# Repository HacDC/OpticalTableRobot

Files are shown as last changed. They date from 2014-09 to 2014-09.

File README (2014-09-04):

Copyright (C) 2013 mirage335
See the end of the file for license conditions.
See license.txt for OpticalTableRobot license conditions.

mirage335-site.dyndns.org

Advanced multi-tool factory based on OpenRail.

Intended to simultaneously operate multiple milling, laser, extrusion (FDM 3D Printing), and inkjet (powder 3D printing, 2D coloring) tools.

See render.png for assembly overview, or download free eDrawings viewer for further investigation.

Comparable to FlexReplicator, but on a massive scale with enhanced precision, thanks to HacDC's 800lbs OpticalTable. This is the kind of machine one might use to 3D print large herringbone power transmissions for lost PLA casting, or carry out a VLSI production run.

Mechanical loads are expected to be far below the table's damage threshold, allowing it to remain aligned to optical tolerances.

__FutureWork__
Openbuilds has intriguing ACME high-pitch threaded rod actuators. Unfortunately, no allowance for anti-backlash is made, so these are unlikely to be used.

Standard timing belts may prove inadeuate for such a large ultra-precise machine. Vectran rope is a possibe substitute.

OpenBuilds has discontinued hardcoat aluminum rails in favor of polycarbonate wheels. While little if any performance degradation is expected, these substitutions need to be reflected in CAD model materials and BOM data.

Supply chain issues are common to many parts in the BOM, secondary suppliers should be added.

__ReprapStatus__
Similarly to the FlexReplicator, a few 3D printed plastic brackets are used, and may be self-replicated. As rigidity was a primary concern, most components are metal, and not 3D printable.

However, unlike other RepRaps, this platform was explicitly designed for a variety of functionality, including CNC milling, PCB manufacture, and even semiconductor fabrication. Theoretically, one might manufacture intermediate equipment (eg. aluminum extruder, lathe).

__Copyright Extensions__
Files embedded into the design by mirage335 with a less restrictive license than GPLv3 place any derrived works under that license. This is definied to include any files pulled into the repository by mirage335 .

__Copyright__
This file is part of OpticalTableRobot.

OpticalTableRobot is free software: you can redistribute it and/or modify
it under the terms of the GNU General Public License as published by
the Free Software Foundation, either version 3 of the License, or
(at your option) any later version.

OpticalTableRobot is distributed in the hope that it will be useful,
but WITHOUT ANY WARRANTY; without even the implied warranty of
MERCHANTABILITY or FITNESS FOR A PARTICULAR PURPOSE.  See the
GNU General Public License for more details.

You should have received a copy of the GNU General Public License
along with OpticalTableRobot.  If not, see <http://www.gnu.org/licenses/>.

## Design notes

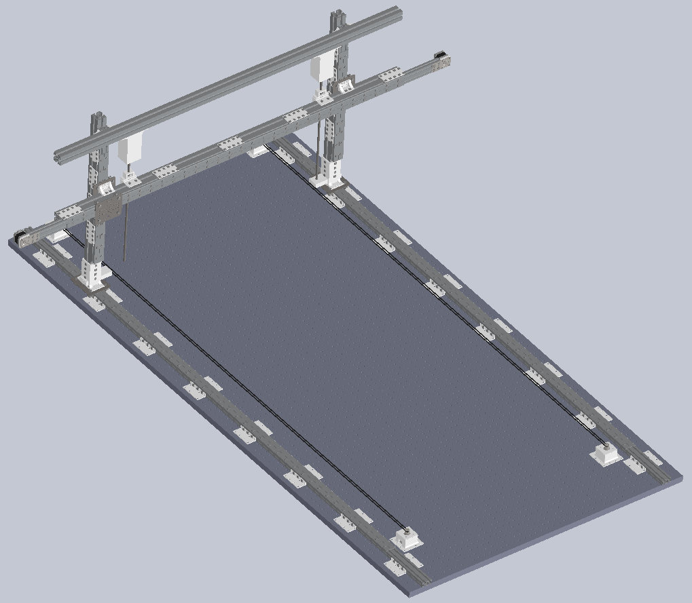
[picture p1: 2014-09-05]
Render.png

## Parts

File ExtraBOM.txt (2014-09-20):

75ft * http://openbuildspartstore.com/gt2-2mm-timing-belt/
3 * http://openbuildspartstore.com/belt-crimp-clamp/
3 * http://openbuildspartstore.com/belt-tension-torsion-spring/

Limit switches and associated brackets (not part of CAD model).

Scrap wood, threaded rod, bearings, spool (optional spool holder).

Various tools (eg. FDM extruder).

PCB heater and pyrex glass surface (heated FDM build platform).

RAMPS controller.

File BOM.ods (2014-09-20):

ITEM NO. | PART NUMBER | DESCRIPTION | QTY. | Cost
1 | OpticalTable |  | 1 |  | 0
2 | TableMount |  | 4 |  | 0
3 | TableMount |  | 4 |  | 0
4 | NEMA17.A.1 | http://openbuildspartstore.com/ nema-17-stepper-motor/ | 8 | 17.5 | 140
5 | GT2_Pulley | http://openbuildspartstore.com/ gt2-2mm-aluminum-timing- pulley-20/ | 6 | 5 | 30
6 | OpenRail | http://openbuildspartstore.com/ openrail-black-anodized/ | 8 | 5 | 40 | 1m
7 | M5_10mm_TeeNut | http://openbuildspartstore.com/ tee-nuts-30-pack/ | 900 | 0.17 | 153
8 | M5x8-Screw | http://openbuildspartstore.com/ low-profile-screws-m5-30-pack/ | 420 | 0.17 | 71.4
9 | M5x25-Screw | 25mm - http://openbuildspartstore.com/ low-profile-screws-m5-30-pack/ | 20 | 0.2 | 4
10 | M5-Washer | http://openbuildspartstore.com/ precision-shim-10x5x1mm/ | 40 | 0.25 | 10
11 | V-Wheel | http://openbuildspartstore.com/ openbuilds-dual-v-wheel-metal/ | 20 | 3.5 | 70 | Replace! Polycarb!
12 | 6252RS_CircularBear ings | http://openbuildspartstore.com/ ball-bearing/ | 40 | 1 | 40
13 | BlankSpacer | http://openbuildspartstore.com/ aluminum-spacers-sizes-1-8-1-1- 2/ | 20 | 0.3 | 6 | 6mm
14 | M5-Nut | http://openbuildspartstore.com/ nylon-insert-hex-locknut-5mm/ | 20 | 0.15 | 3
15 | 40mmBracket | 40mm - http://openbuildspartstore.com/ openrail-gantry-plate-universal- mount/ | 5 | 8 | 40
16 | 20_20x40x1830 | 80/20 20 SERIES 20-2040 20mm X 40mm T-SLOTTED EXTRUSION x 1830mm | 1 | 22.08 | 22.08
17 | 20_20x40x2440 | 80/20 Inc., 20-2040, 20 Series, 20mm x 40mm T-Slotted Extrusion x 2440mm | 2 | 28.79 | 57.58
18 | TableAdapter |  | 32 |  | 0
19 | M5-Screw | M5x8 | 416 | 0.17 | 70.72
20 | 40seriesVerticalAda pter |  | 2 | 8 | 16
21 | M5-Screw | M5x14 | 32 |  | 0
22 | 20_20x40x610 | 80/20 20 SERIES 20-2040 20mm X 40mm T-SLOTTED EXTRUSION x 610mm | 2 | 8.66 | 17.32
23 | GenericExtrusion |  | 2 |  | 0
24 | GenericExtrusion |  | 2 |  | 0
25 | Belt3-2^Robot |  | 2 |  | 0
26 | 40seriesVerticalAda pter |  | 2 | 8 | 16
27 | OpenRail | http://openbuildspartstore.com/ openrail-black-anodized/ | 4 | 2.5 | 10 | 0.5m
28 | 40seriesHorizontalAd apter |  | 2 | 8 | 16
29 | M5-Screw | M5x12 | 32 | 0.17 | 5.44
30 | 20-40series |  | 6 |  | 0
31 | 20-40series |  | 26 |  | 0
32 | OpenRail | http://openbuildspartstore.com/ openrail-black-anodized/ | 2 | 9 | 18 | 1.5m
33 | motor_mount_plate | http://openbuildspartstore.com/ motor-mount-plate/ | 2 | 6.95 | 13.9
34 | MotorSpacer | 3D Printed | 2 | 0 | 0
35 | M3x15-Screw | http://www.amazon.com/Metric -15mm-Socket-Screw- Black/dp/B004MFF4E6/ref=sr_1_1 1?ie=UTF8&qid=1407275148&sr=8 -11&keywords=M3+15mm+screw | 8 | 0.53 | 4.24
36 | StepperBracket | 3D-Printed | 2 | 0 | 0
37 | StepperBracket | 3D-Printed | 2 | 0 | 0
38 | FlexibleCoupling | http://openbuildspartstore.com/ 1-4-x-5mm-flexible-coupling/ | 2 | 5.95 | 11.9
39 | 608zz_CircularBearin gs | http://seemecnc.com/products /608zz-ball-bearing | 4 | 1.25 | 5
40 | M8_Bolt | http://www.mcmaster.com/#94 150a355/=t5xoba | 12 | 0.27 | 3.24
41 | M8ThreadedRod | http://www.mcmaster.com/#sta ndard-threaded-rods/=t5xlek | 2 | 12.86 | 25.72
42 | Z-Axis_Gripper | 3D Printed | 2 | 0 | 0
43 | Z-Axis_Gripper | 3D Printed | 2 | 0 | 0
 |  |  |  |  | 920.54

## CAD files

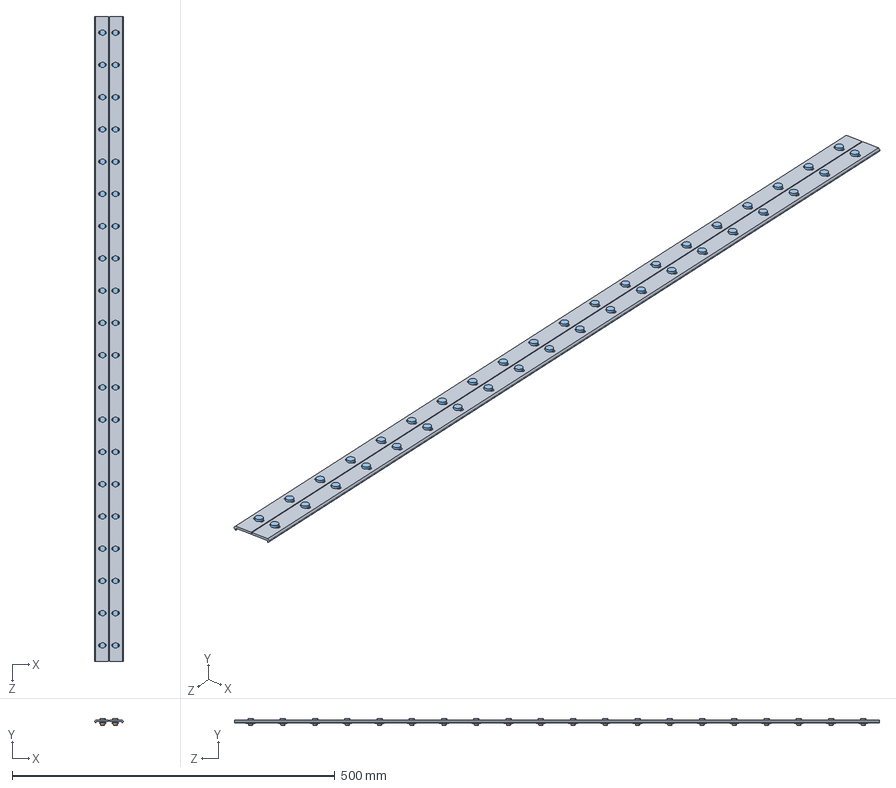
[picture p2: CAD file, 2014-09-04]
Resources/Motion/Linear/OpenRail/20_20x40_OpenRail.SLDASM
45.1 x 10.8 x 1000.0 mm
OpenRail x 2
M5_10mm_TeeNut x 40
M5x8-Screw x 40

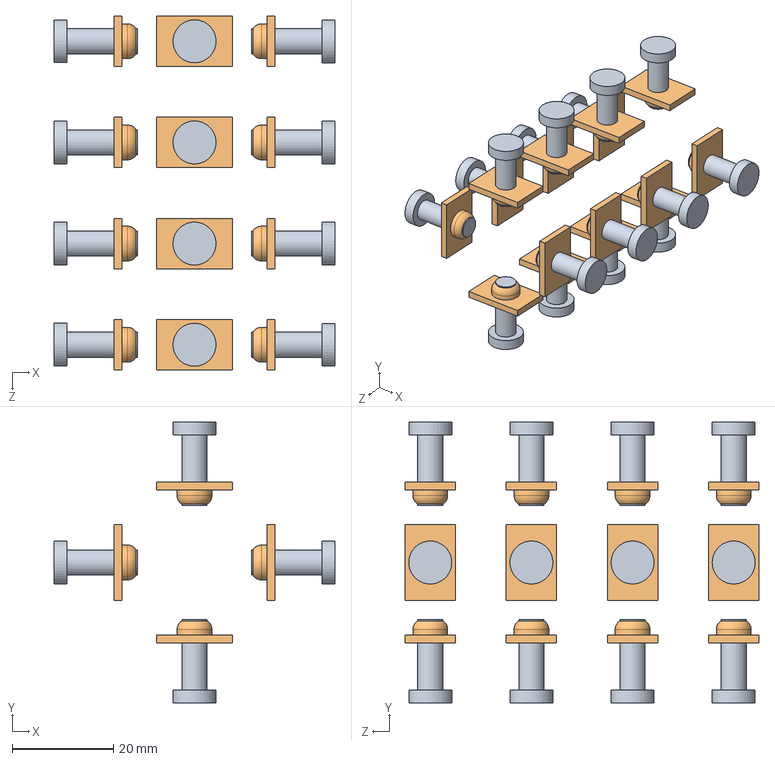
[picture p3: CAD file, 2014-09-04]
Resources/Motion/Linear/OpenRail/Bracket/40seriesVerticalAdapter.SLDASM
55.5 x 55.5 x 70.0 mm
M5-Screw x 16
M5_10mm_TeeNut x 16

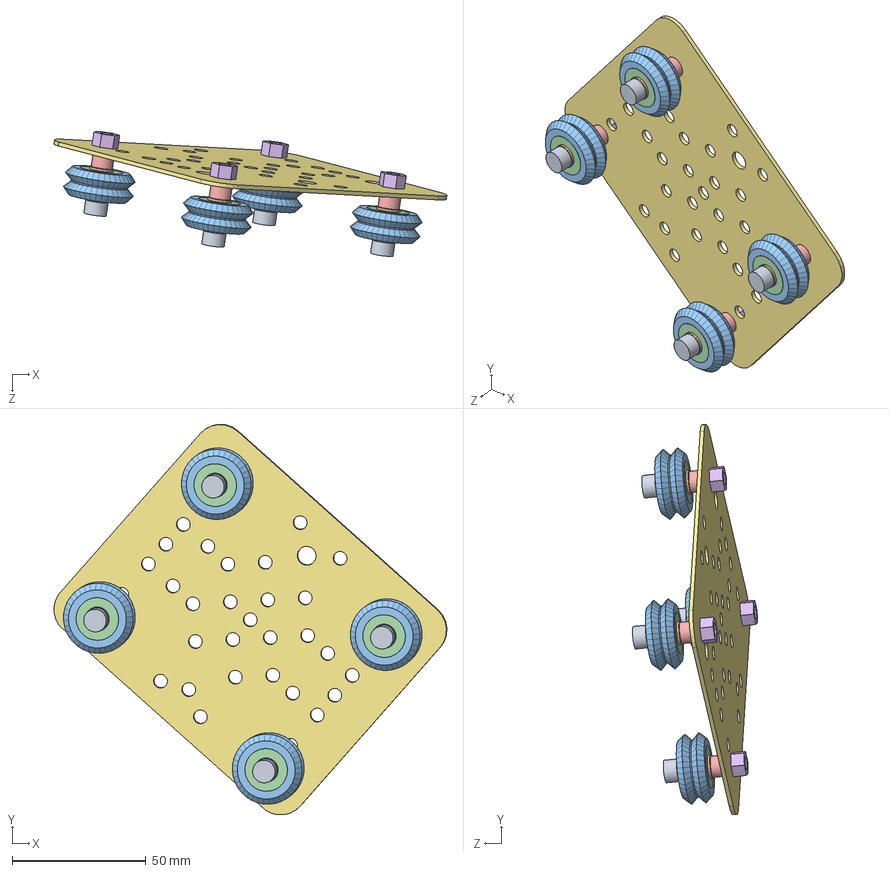
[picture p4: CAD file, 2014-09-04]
Resources/Motion/Linear/OpenRail/Carriage/Carriage.SLDASM
146.6 x 145.7 x 46.7 mm
M5x25-Screw x 4
M5-Washer x 8
V-Wheel x 4
6252RS_CircularBearings x 8
BlankSpacer x 4
M5-Nut x 4
40mmBracket

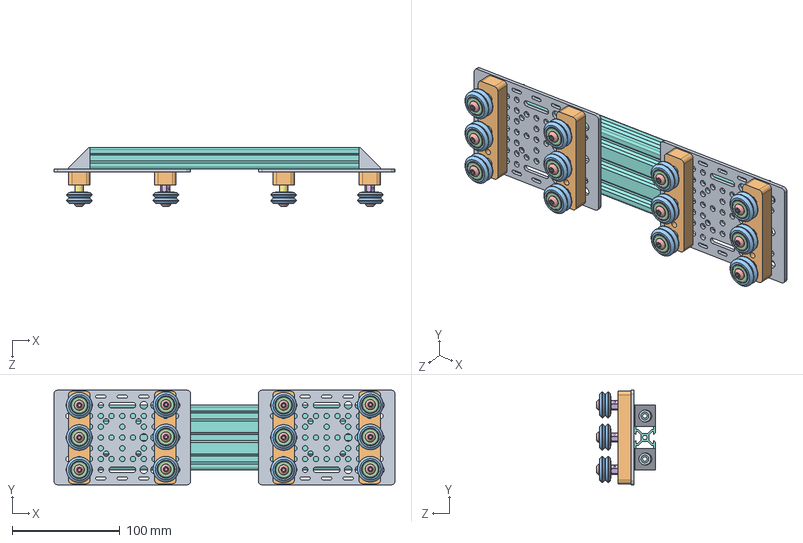
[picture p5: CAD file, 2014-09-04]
Resources/Motion/Linear/OpenRail/OpenBuilds/V-Slot Solid Works/traverse_250.SLDASM
317.0 x 88.0 x 55.1 mm
universal_plate x 2
spacer_block x 4
dual_v_wheel x 12
ball_bearing x 24
socket button head screw_iso x 12
eccentric_spacer x 6
aluminium_spacer x 6
extrusion_20x60x250
corner_connector_90deg x 4

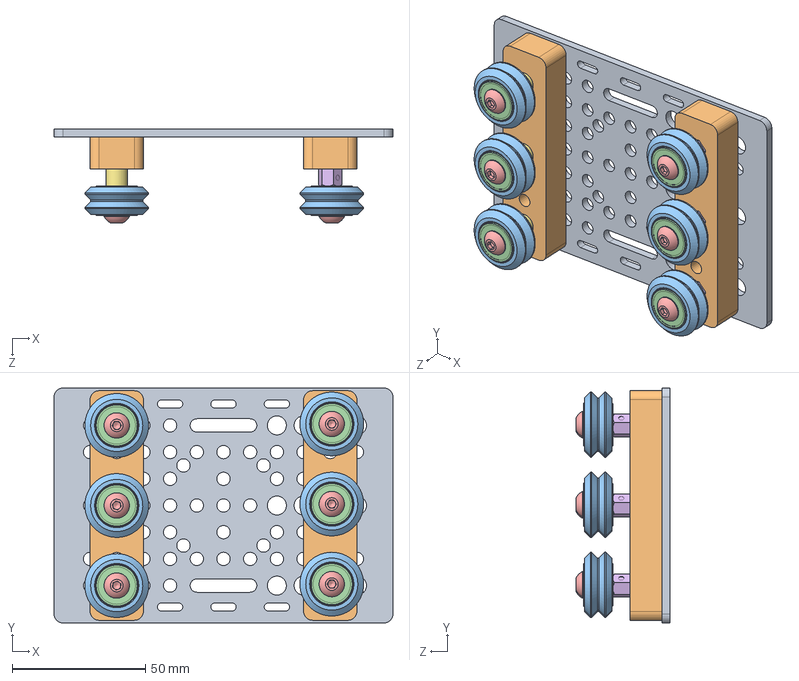
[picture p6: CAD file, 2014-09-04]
Resources/Motion/Linear/OpenRail/OpenBuilds/V-Slot Solid Works/Wheels/chariot.SLDASM
127.0 x 88.0 x 35.1 mm
universal_plate
spacer_block x 2
dual_v_wheel x 6
ball_bearing x 12
socket button head screw_iso x 6
eccentric_spacer x 3
aluminium_spacer x 3

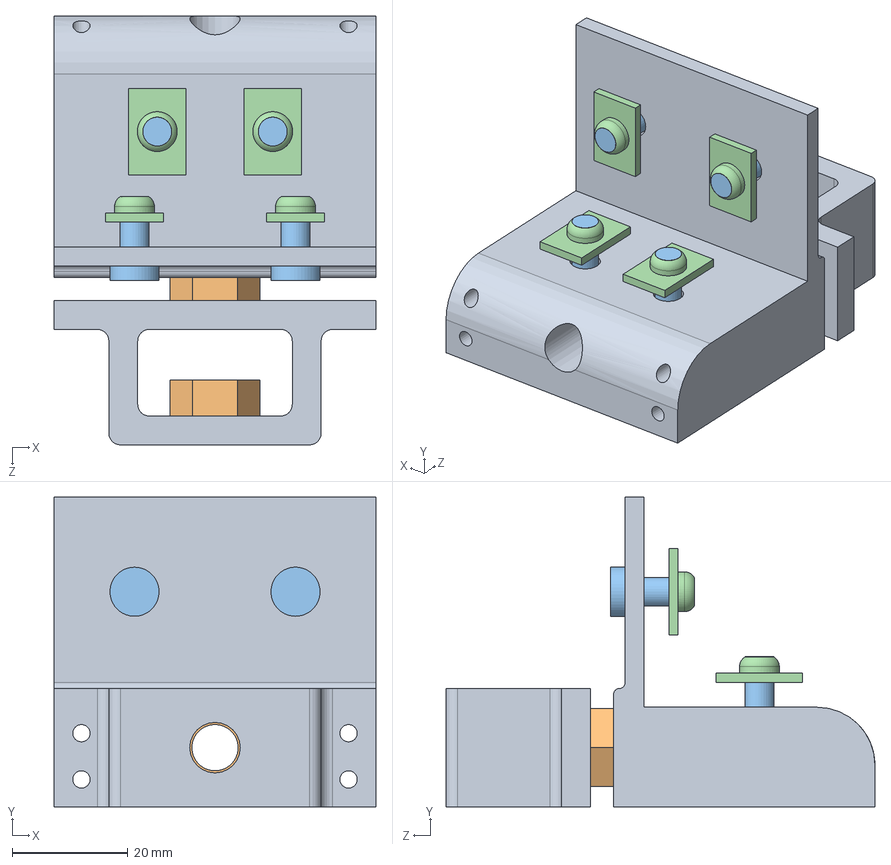
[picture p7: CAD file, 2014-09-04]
Resources/Motion/Rotary/Z-Axis_ThreadedRodDrive/Gripper/Z-Axis_Gripper.SLDASM
55.8 x 53.6 x 74.2 mm
Z-Axis_Gripper x 2
M8_Bolt x 2
M5-Screw x 4
M5_10mm_TeeNut x 4

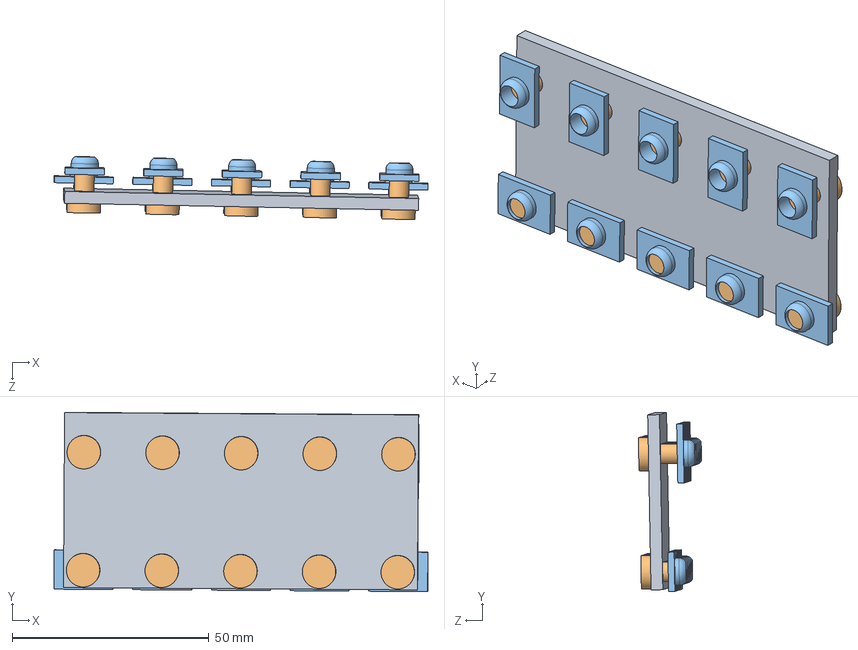
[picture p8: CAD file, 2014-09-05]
Resources/Structure/Brackets/20-40series.SLDASM
95.1 x 45.6 x 16.0 mm
20-40series
M5-Screw x 10
M5_10mm_TeeNut x 10

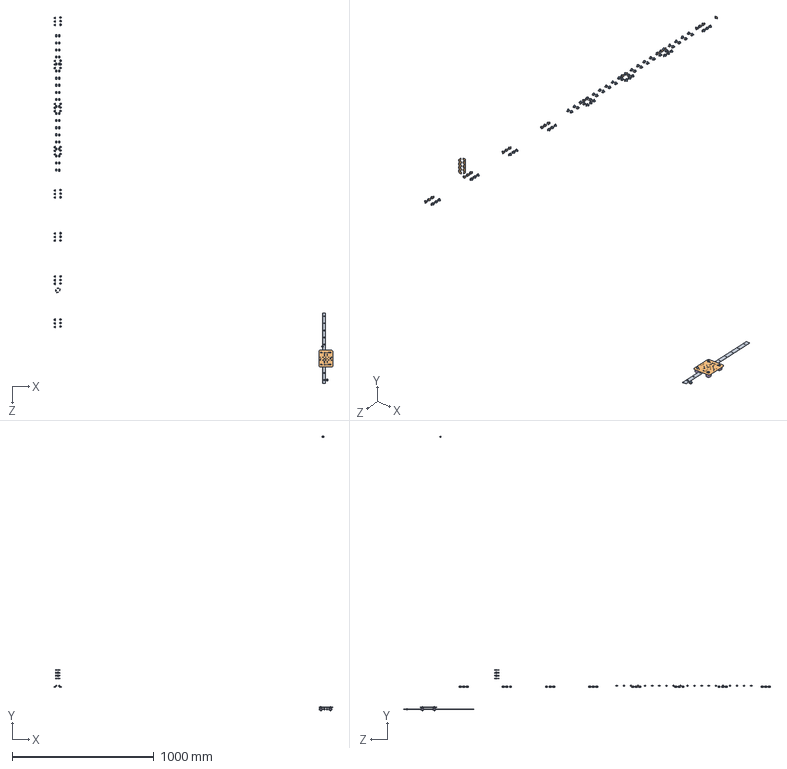
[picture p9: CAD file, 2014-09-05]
Resources/Subunits/Slides/20x40.SLDASM
1971.1 x 1941.7 x 2593.7 mm
OpenRail
M5_10mm_TeeNut x 144
M5x8-Screw x 80
M5x25-Screw x 4
M5-Washer x 8
V-Wheel x 4
6252RS_CircularBearings x 8
BlankSpacer x 4
M5-Nut x 4
40mmBracket
M5-Screw x 48

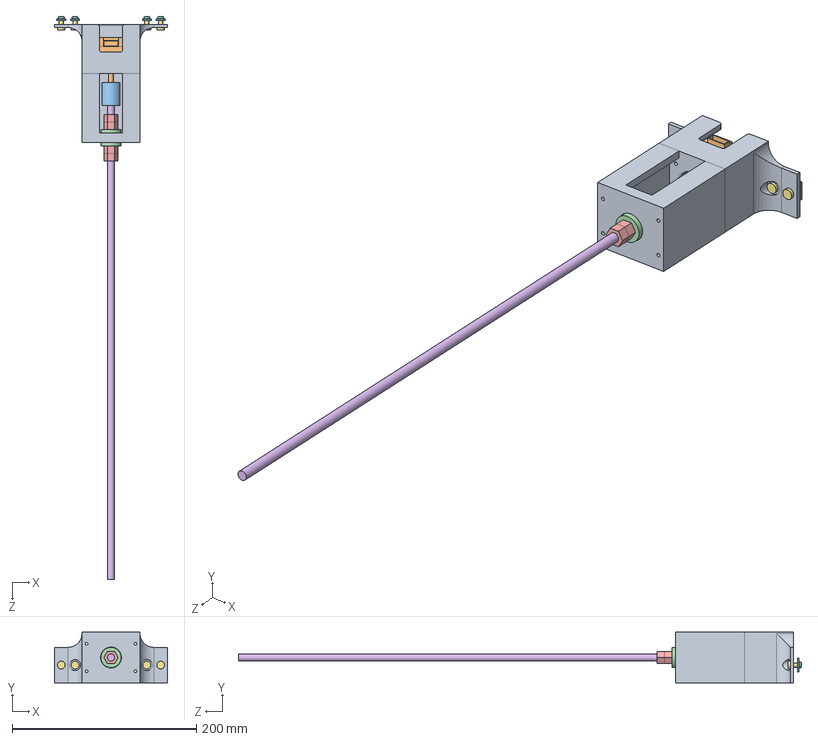
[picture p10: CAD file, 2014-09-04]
Resources/Subunits/Thrusters/40seriesThreadedRodDrive.SLDASM
123.0 x 55.0 x 611.8 mm
StepperBracket x 2
NEMA17.A.1
FlexibleCoupling
608zz_CircularBearings x 2
M8_Bolt x 4
M8ThreadedRod
M5-Screw x 4
M5_10mm_TeeNut x 4

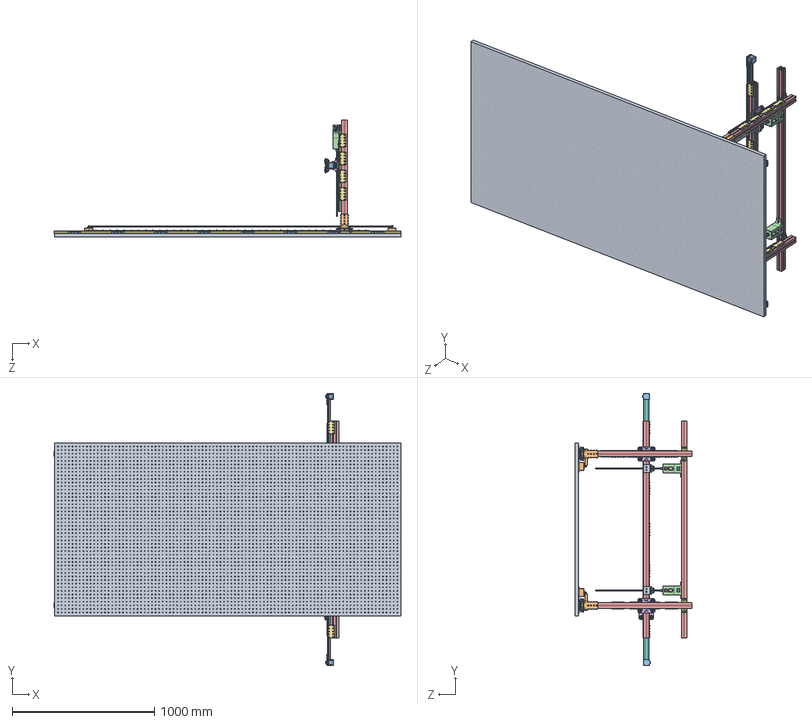
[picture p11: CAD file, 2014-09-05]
Robot.SLDASM
2441.6 x 1914.8 x 826.2 mm
OpticalTable
TableMount x 8
NEMA17.A.1 x 8
GT2_Pulley x 6
OpenRail x 14
M5_10mm_TeeNut x 700
M5x8-Screw x 268
M5x25-Screw x 20
M5-Washer x 40
V-Wheel x 20
6252RS_CircularBearings x 40
BlankSpacer x 20
M5-Nut x 20
40mmBracket x 5
20_20x40x2440 x 2
TableAdapter x 32
M5-Screw x 432
40seriesVerticalAdapter x 4
Belt3-2^Robot x 2
20_20x40x610 x 2
GenericExtrusion x 4
40seriesHorizontalAdapter x 2
20-40series x 32
20_20x40x1830
motor_mount_plate x 2
MotorSpacer x 2
M3x15-Screw x 8
StepperBracket x 4
FlexibleCoupling x 2
608zz_CircularBearings x 4
M8_Bolt x 12
M8ThreadedRod x 2
Z-Axis_Gripper x 4

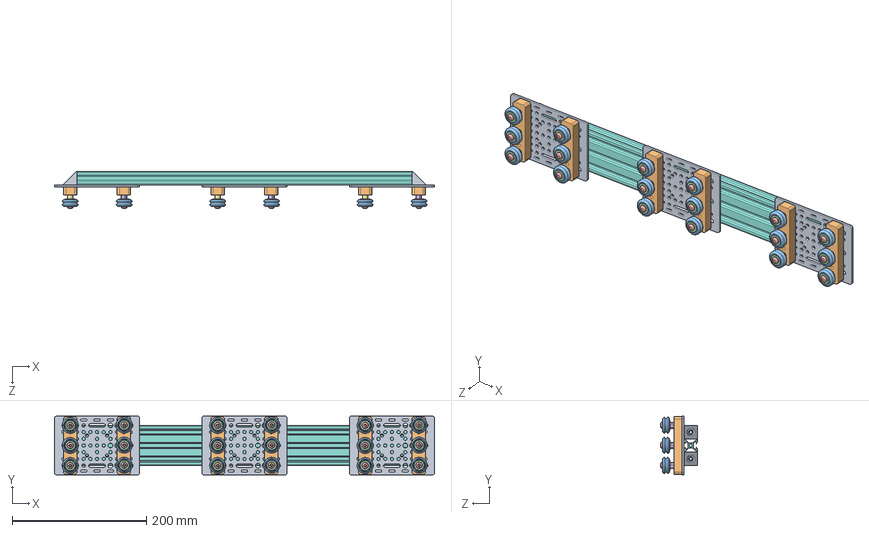
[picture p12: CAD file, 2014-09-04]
Resources/Motion/Linear/OpenRail/OpenBuilds/V-Slot Solid Works/traverse.SLDASM
567.0 x 88.0 x 55.1 mm
universal_plate x 3
spacer_block x 6
dual_v_wheel x 18
ball_bearing x 36
socket button head screw_iso x 18
eccentric_spacer x 9
aluminium_spacer x 9
extrusion_20x60x500
corner_connector_90deg x 4

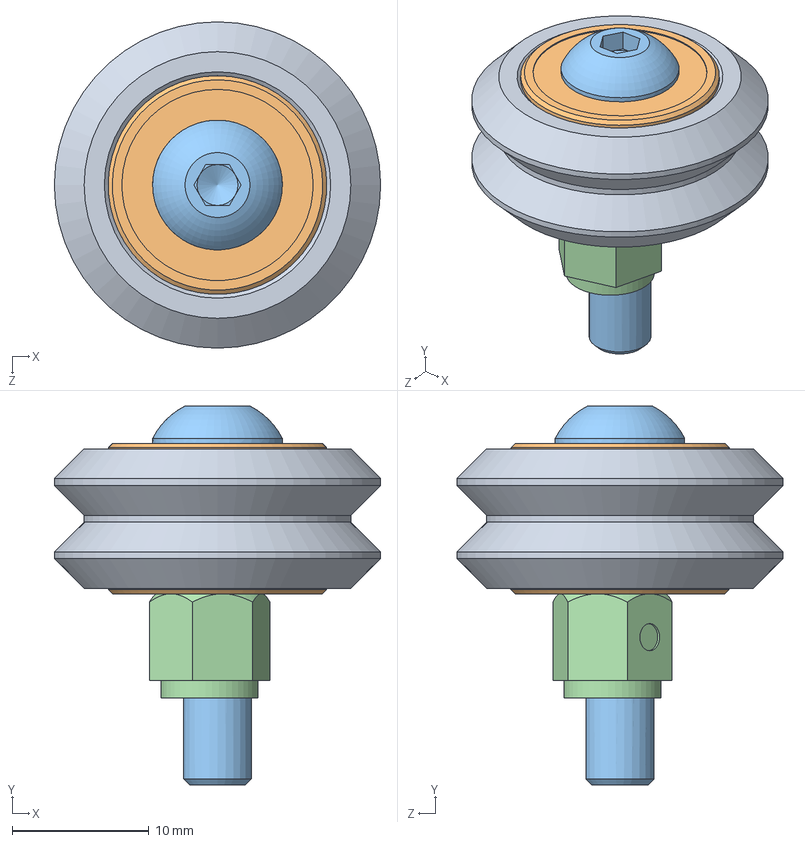
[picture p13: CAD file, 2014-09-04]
Resources/Motion/Linear/OpenRail/OpenBuilds/V-Slot Solid Works/Wheels/eccentric_wheel.SLDASM
23.9 x 27.8 x 23.9 mm
dual_v_wheel
ball_bearing x 2
socket button head screw_iso
eccentric_spacer

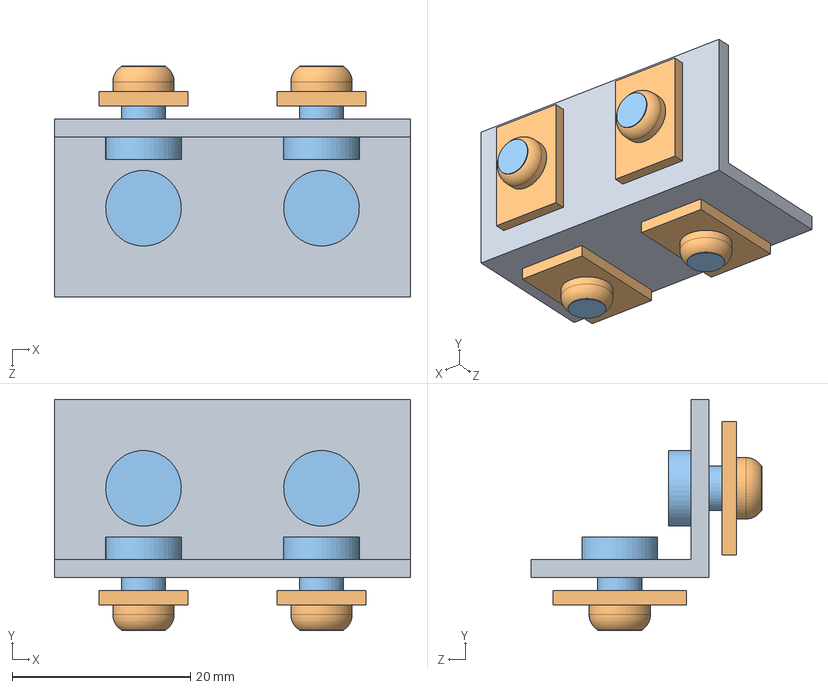
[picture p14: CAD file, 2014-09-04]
Resources/Structure/Brackets/DoubleL.SLDASM
40.0 x 26.0 x 26.0 mm
DoubleL
M5_10mm_TeeNut x 4
M5x8-Screw x 4

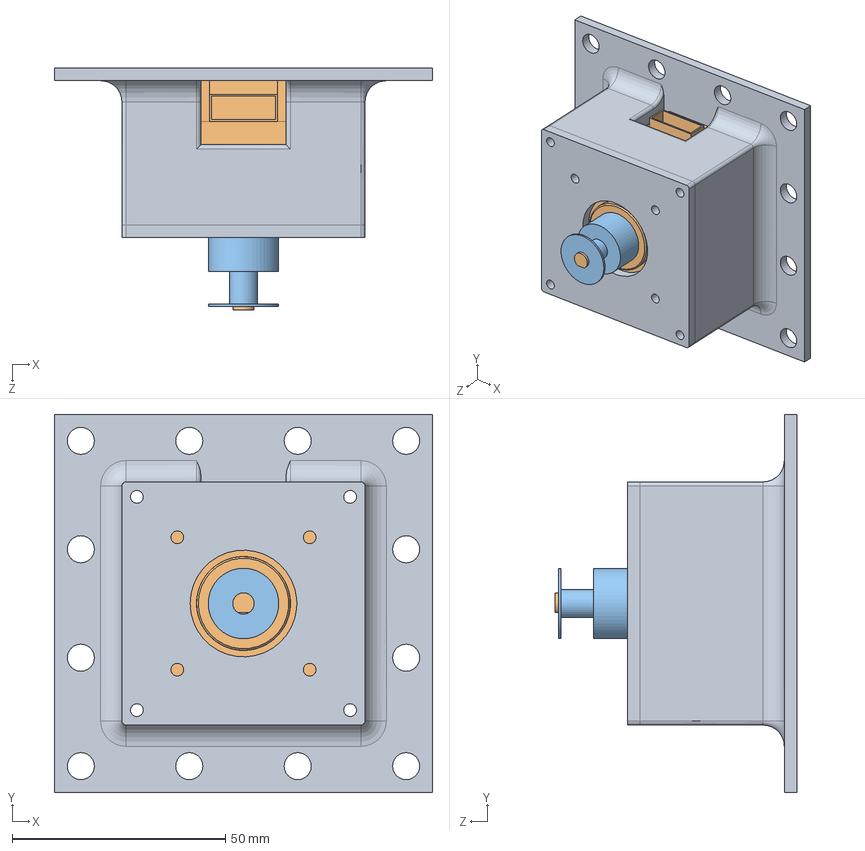
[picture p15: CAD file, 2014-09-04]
Resources/Subunits/Thrusters/TableMountedPulleyDrive.SLDASM
88.6 x 88.6 x 56.8 mm
TableMount x 2
NEMA17.A.1
GT2_Pulley

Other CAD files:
Resources/Motion/Linear/OpenRail/Bearing/WheelBearing.SLDASM
Resources/Motion/Linear/OpenRail/Bracket/40seriesHorizontalAdapter.SLDASM
Resources/Subunits/Thrusters/FloatingPulleyDrive.SLDASM
Resources/Structure/Brackets/TableAdapter.SLDASM
Exports/20-40series.STL
Exports/40seriesVerticalAdapter.STL
Exports/TableAdapter.STL
Resources/Motion/Linear/OpenRail/Bearing/6252RS_CircularBearings.SLDPRT
Resources/Motion/Linear/OpenRail/Bearing/BlankSpacer.SLDPRT
Resources/Motion/Linear/OpenRail/Bearing/EccentricSpacer.SLDPRT
Resources/Motion/Linear/OpenRail/Bearing/M5-Nut.SLDPRT
Resources/Motion/Linear/OpenRail/Bearing/M5-Washer.SLDPRT
Resources/Motion/Linear/OpenRail/Bearing/M5x25-Screw.SLDPRT
Resources/Motion/Linear/OpenRail/Bearing/V-Wheel.SLDPRT
Resources/Motion/Linear/OpenRail/Bracket/40mmBracket.SLDPRT
Resources/Motion/Linear/OpenRail/Bracket/40seriesHorizontalAdapter.SLDPRT
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

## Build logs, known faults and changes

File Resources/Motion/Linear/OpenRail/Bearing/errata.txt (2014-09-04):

V-Wheel model is intentionally not completely accurate, to permit meshing with accurate OpenRail model.

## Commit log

2014-09-04 Z-axis thruster added.
    [20_20x40_OpenRail.SLDASM, 20x40.SLDASM, 40seriesThreadedRodDrive.SLDASM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]
2014-09-04 Z-axis gripper design.
    [40seriesThreadedRodDrive.SLDASM, Robot.SLDASM, StepperBracket.SLDPRT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]
2014-09-04 Anti-backlash Z-Axis gripper.
    [40seriesThreadedRodDrive.SLDASM, Robot.SLDASM, Z-Axis_Gripper.SLDASM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]
2014-09-04 Nuts and bolts.
    [Z-Axis_Gripper.SLDASM]
2014-09-04 Adapter 20-40series brackets in progress.
    [20-40series.SLDASM, 20-40series.SLDPRT, Robot.SLDASM]
2014-09-04 Corner brackets.
    [20-40series.SLDASM, 20-40series.SLDPRT, 20x40.SLDASM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]
2014-09-04 Flat side brackets restored.
    [20-40series.SLDASM, 20x40.SLDASM, Robot.SLDASM]
2014-09-05 Corrected interferences.
    [20-40series.SLDASM, 20x40.SLDASM, Robot.SLDASM]
2014-09-05 Rudimentary BOM.
    [BOM.ods]
2014-09-20 BOM eratta.
    [BOM.ods]
2014-09-20 M5 screw sizes added to BOM properties, more BOM eratta.
    [BOM.ods, M5-Screw.SLDPRT]
2014-09-20 ExtraBOM and more BOM eratta.
    [BOM.ods]
2014-09-20 BOM bugfix.
    [BOM.ods]
2014-09-20 Regenerated BOM.
    [BOM.ods]
2015-02-27 Exported STL files.
    [20-40series.STL, TableAdapter.STL]
2015-02-27 Vertical adapter exported STL file.
    [40seriesVerticalAdapter.STL]
